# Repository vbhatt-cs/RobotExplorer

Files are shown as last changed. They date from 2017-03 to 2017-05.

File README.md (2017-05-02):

# Scout Car for Automatic Mapping

Scout car for automatic mapping is a bot which can explore and map an area automatically.

## Requirements

### Hardware
  * Arduino WeMos D1 R2 (any arduino with WiFi shield works but pin mapping and arduino code will change)
  * 12V battery
  * 2 DC motors + wheels
  * L298N motor driver
  * Wheel encoder with IR sensor 
  * IR proximity sensor 
  * MPU 9250 9-dof imu sensor
  * Chassis to mount the components
  
### Software
  * Arduino IDE - https://www.arduino.cc/en/main/software
  * Optional - Microsoft Visual Studio + Visual Micro - https://www.visualstudio.com/downloads/ http://www.visualmicro.com/page/Arduino-Visual-Studio-Downloads.aspx
  * Python 3.x (tested with 3.6) - https://www.python.org/downloads/
  * socket, parse, numpy, matplotlib libraries
    
Socket is installed by default in most python distributions. For other libraries, use the command 

    pip install <library_name>
    
## Getting Started

First, connect the componenets according to the below diagram

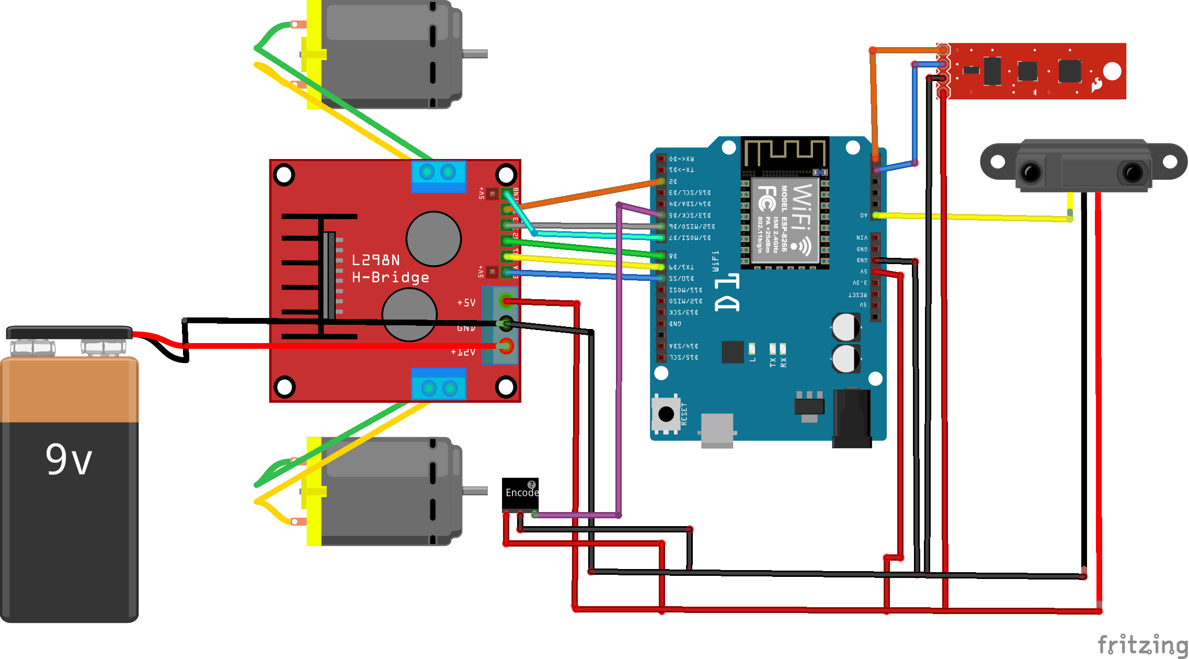
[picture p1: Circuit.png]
Ciruit


Note that the battery should be 12V. The red component on the top right is MPU9250 and the component below it is the IR sensor. The pin numbers on the WeMos might be different from what is given in the diagram. Physically the connections look the same (Ex.: the wire connected to the second pin from the top in the diagram will be connected to the second pin from the top in WeMos)

Once the hardware connections are done, open the [ino file](V1_1_MoveInGivenDirectionWemos/V1_1_MoveInGivenDirectionWemos/V1_1_MoveInGivenDirectionWemos.ino) (if you are using visual studio, open the [visual studio solution](V1_1_MoveInGivenDirectionWemos/V1_1_MoveInGivenDirectionWemos.sln)). Build and upload to the WeMos board (see this [tutorial](http://www.instructables.com/id/Programming-the-WeMos-Using-Arduino-SoftwareIDE/) if you haven't programmed WeMos before).

Now, connect to WeMos wifi network from your PC and run the [main python script](PCSide/main.py). If everything works fine, you should be seeing the bot moving around and a map being generated on the PC. After exploration, the map will be saved in the same folder ([Example](PCSide/map.png)). If there is some problem, see the troubleshooting section.

## Troubleshooting

1. **No WiFi network of WeMos**: Check if the bot is on and LED of the WiFi shield in WeMos is glowing. If not, reset WeMos and check again. If it still doesn't work, then try uploading the [WeMos Web Server](TempCodes/Wemos_WebServer) project and check if it works. If it fails then there is some problem with the WiFi shield.

2. **The bot continuously rotates in one place or it doesn't move in the right direction**: The magnetometer is most probably not calibrated properly. Upload the [Calibration](TempCodes/MPU9250_Yaw) project and open the serial monitor. Reset WeMos and move the bot in shape of 8 (like during compass calibration in phones) or just rotate around all 3 axes (*Note that the calibration needs to be done away from strong magnets and when the magnetometer is mounted on the bot*). After a while, the yaw values will be displayed in the serial monitor. Check if they are correct. If so, copy the bias, scale values to the main ino file (into magBias and magScale). If not, reset and try again. 

    In case the calibration fails after multiple attempts, print mx, my, mz values from magnetometer and copy them to an excel sheet. Find min, max value of mx, my, and mz. Find bias = (max + min)/2 and scale = (max - min)/2 for x, y, and z. 
    Calculate x' = (x - biasX)/scaleX, and similarly y' and z'. Scatter plot x', y', z' pairwise and check if they are points in the interior of a unit circle. If so, then use the bias, scale values. Else, repeat the calibration.
    
    In the unlikely case that the yaw values are not stable, change the values of Kp, Ki in MahonyQuaternionUpdate function till it gives stable values quickly and then do the calibration.
    
3. **The bot stops (and detects wall) even if the wall is far**: Check the trigger range of IR proximity sensor and set it such that the bot has enough space to rotate after detecting the wall. IR proximity sensor is known to give bad readings in the presence of sunlight. So it is better to block sunlight during mapping. If you need to bot to map outdoor environment, then a different sensor should be used to detect walls.

4. **The bot moves very near/ very far at a time**: Set the CELL_DIS in [maparray.py](PCSide/maparray.py) higher/lower.

5. **The bot doesn't map the full area**: Set the MAP_SIZE to a higher value.
    
4. **The bot moves very slowly/ one of the wheels doesn't turn**: The battery is getting discharged. Replace/recharge them. 

5. **UDP connection times out**: It may happen due to multiple reasons. First, open the serial monitor and reset WeMos to see whether it is creating a WiFi hotspot. Also, check if the IP address of WeMos is same as the one written in [communication.py](PCSide/communication.py) and run again. Second, replace/recharge the battery. Third, in [main.py](PCSide/main.py), increase the delay such that the bot is able to move and stop before a new UDP request is sent by the PC (5 seconds is generally enough) and run again. If neither of the methods work, then the reason is unknown.

## Known issues

1. WeMos doesn't reset when it is connected to the encoder (through D3 pin). A temporary fix is to remove the connection, reset the board and connect the encoder afterwards.

2. Connection between PC and bot times out sometimes. The timeout is extremely rare when the battery is fully charged and there are no other strong WiFi networks in the surrounding. Other observations were - 
    * Timeouts are less frequent when the delay between two consecutive requests by the PC is high
    * More timeouts when an UDP packet reaches arduino while the motor is moving
    * No timeouts when only UDP communication is taking place (no sensors/motor)
    * No timeouts when encoder is removed (not fully tested - might just be coincidence)

3. There are oscillations when the bot rotates in place. This can be solved by turning the bot slowly so that there is no overshoot.

4. The bot can deviate from its path due to incorrect rotation/movement.

5. If the bot deviates a bit and wrongly detects a wall (physically) in the cell (of the map) which it had previously detected as open, then the bot gets stuck there and the mapping doesn't continue.

6. If the proximity sensor fails to detect a wall (due to not being in the line of sight) and the bot crashes into it, it can't recover and continue mapping.

## Future work

1. **Solving existing issues**: Using a motor with finer speed control solves the first issue. The second issue is solved partially by using encoders in addition to magnetometer for rotation and is fully solved if the PC code is able to detect wrong movement and correct it. The third issue won't occur if the bot movement is correct. Fourth issue can be solved by adding more sensors around the bot (it still can't recover from physical crashes)

2. **Reducing power consumption**: Right now, the exact power usage is not calculated and the hardware/code is not optimized for minimum power consumption. It will be necessary since the bot should be able to map the required area in a single charge.

3. **Mapping/Exploration which doesn't depend on accurate movement**: The idea of this bot may be used for applications like cleaning the house where it may not be possible to move the bot accurately due to its size. Also, the resolution of the map will be bad if the bot is assumed to be smaller than or equal to one cell size. Hence, the bot needs to be able to explore/map in arbitrary directions.

4. **Dynamic updation of map**: Right now, the bot assumes the area to map as static and generates a map. But in reality, there may be obstacles which are moved around and hence, the map needs to be changed dynamically.

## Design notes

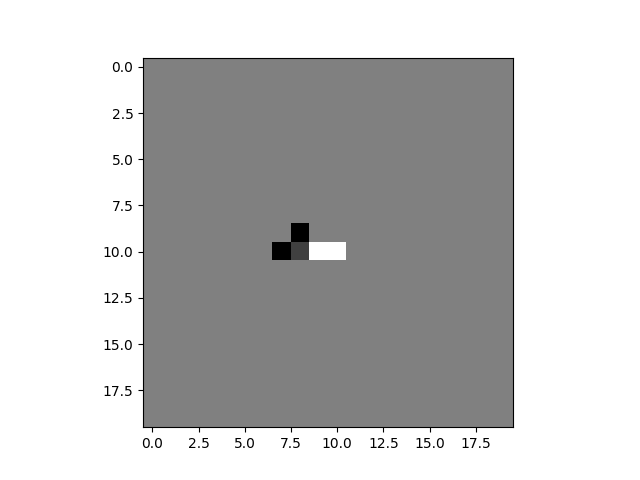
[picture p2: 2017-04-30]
PCSide/map.png

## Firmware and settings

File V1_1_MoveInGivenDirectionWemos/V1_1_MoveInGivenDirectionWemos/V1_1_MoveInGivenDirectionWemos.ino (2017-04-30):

/*
Name:		V1_1_MoveInGivenDirectionWemos.ino
Created:	3/11/2017 11:35:00 AM
Author:	Varun Bhatt
*/

#include <PID_v1.h>				//Arduino PID library
//For magnetometer
#include <Wire.h>
#include <FaBo9Axis_MPU9250.h>
//For web server
#include <ESP8266WiFi.h>
#include <WiFiUdp.h>

//Set to 1 if debugging in serial
const bool DEBUG_SERIAL = 1;

// Pins used on Wemos D1 R2
#define LPWM D8
#define LDIR1 D7
#define LDIR2 D6

#define RPWM D5
#define RDIR1 D4
#define RDIR2 D0

#define ENCODER D3

#define PROXIMITY A0

// Left and Right steady state speed
const int RIGHT_SS_SPEED = 300;
const int LEFT_SS_SPEED = 300;
const int CONSTRAIN_LOW = 250;
const int CONSTRAIN_HIGH = 350;

// Left and Right speed
int rightSpeed = 300;
int leftSpeed = 300;

//PID Values
double curDirection = 0, output;

// PID Multipliers
float kp = 1;
float ki = 0;
float kd = 0.2;

double setDirection = 0;	//Reference direction
int setDistance = 0;		//Reference distance

int curDistance = 0;
bool runMotor = true;
bool rotateMotor = true;
bool wall = false;
bool startFlag = true;

FaBo9Axis fabo_9axis;	// For MPU9250 readings
float q[4] = { 1.0f, 0.0f, 0.0f, 0.0f };    // vector to hold quaternion
float eInt[3] = { 0.0f, 0.0f, 0.0f };       // vector to hold integral error for Mahony method
float deltat = 0.0f;						// integration interval for both filter schemes
uint32_t lastUpdate = 0;	// used to calculate integration interval
uint32_t Now = 0;							// used to calculate integration interval
uint32_t startTime = 0;
float magBias[3] = { 7.49, 3.28, -18.94};
float magScale[3] = { 39.96, 41.53, 33.60};

//Setup PID
PID wheelControl(&curDirection, &output, &setDirection, kp, ki, kd, DIRECT);

//SSID of access point
const char *SSID = "Wemos";
const char *password = "qwer321!";

//UDP stuff
WiFiUDP Udp;
//IPAddress ip(192, 168, 137, 69);
//IPAddress gateway(192, 168, 137, 1);
//IPAddress subnet(255, 255, 255, 0);
unsigned int localUdpPort = 4210;  // local port to listen on

void setup() {
	if (DEBUG_SERIAL)
		Serial.begin(9600);

    pinMode(ENCODER, INPUT);
    attachInterrupt(digitalPinToInterrupt(ENCODER), encISR, FALLING);

	pinMode(RPWM, OUTPUT);
	pinMode(RDIR1, OUTPUT);
	pinMode(RDIR2, OUTPUT);

	pinMode(LPWM, OUTPUT);
	pinMode(LDIR1, OUTPUT);
	pinMode(LDIR2, OUTPUT);

	pinMode(PROXIMITY, INPUT);

	//Start the WiFi access point
	if (DEBUG_SERIAL)
	{
		Serial.println();
		Serial.print("Configuring access point...");
	}

	WiFi.softAP(SSID);
	/*WiFi.begin(SSID, password);
	WiFi.config(ip, gateway, subnet);

	while (WiFi.status() != WL_CONNECTED) {
		delay(500);
		if (DEBUG_SERIAL)
			Serial.print(".");
	}*/

	Udp.begin(localUdpPort);

	if (DEBUG_SERIAL)
		Serial.printf("Now listening at IP %s, UDP port %d\n", WiFi.softAPIP().toString().c_str(), localUdpPort);
    
	//Stop the motor initially
	digitalWrite(LDIR1, LOW);
	digitalWrite(LDIR2, LOW);
	analogWrite(LPWM, 0);
	digitalWrite(RDIR1, LOW);
	digitalWrite(RDIR2, LOW);
	analogWrite(LPWM, 0);

	//Initialize MPU9250
	fabo_9axis.begin();

	//turn the PID on
	wheelControl.SetOutputLimits(-1000, 1000);
	wheelControl.SetMode(AUTOMATIC);

	startTime = micros();
}

void loop() {
	handleUDP();	//Handle UDP messages

	//Read MPU9250 and get compass heading
	Now = micros();
	deltat = ((Now - lastUpdate) / 1000000.0f); // set integration time by time elapsed since last filter update
	lastUpdate = Now;
	
	curDirection = getYaw();
	if (curDirection < -170)
		curDirection = abs(curDirection);

	runMotor = curDistance < setDistance;

	if (rotateMotor)
		wall = false;
	else
		wall = analogRead(PROXIMITY) < 512;

	//Compute the PID output
	wheelControl.Compute();

	if (DEBUG_SERIAL)
	{
		Serial.print(" yaw = "); Serial.println(curDirection);
		Serial.print(" ref = "); Serial.println(setDirection);
		Serial.print(" output = "); Serial.println(output);
		Serial.print(" distance = "); Serial.println(curDistance);
	}

	//Set the PWM values for the motor
	//
	//Output added to one wheel and subtracted from another wheel to rotate the bot
	//Change the sign of output (if needed) to make the bot rotate in a direction which reduces the error. 
	//
	//The motor was not moving for PWM below CONSTRAIN_LOW and moving too fast for PWM over CONSTRAIN_HIGH
	//So constrain the value inside that range
	rightSpeed = RIGHT_SS_SPEED + output;
	rightSpeed = constrain(rightSpeed, CONSTRAIN_LOW, CONSTRAIN_HIGH);

	leftSpeed = LEFT_SS_SPEED - output;
	leftSpeed = constrain(leftSpeed, CONSTRAIN_LOW, CONSTRAIN_HIGH);

	if (runMotor && !wall)	//Start the motor
	{
		if (micros() - startTime < 8000000)
		{
			analogWrite(RPWM, 0);
			analogWrite(LPWM, 0);
		}

		else if ((abs(setDirection - curDirection) > 5 && abs(setDirection - curDirection) < 355) && rotateMotor)
		{
			if (setDirection - curDirection > 0 && setDirection - curDirection < 180)
			{
				digitalWrite(RDIR2, LOW);
				digitalWrite(RDIR1, HIGH);
				digitalWrite(LDIR2, LOW);
				digitalWrite(LDIR1, HIGH);
				analogWrite(RPWM, RIGHT_SS_SPEED);
				analogWrite(LPWM, LEFT_SS_SPEED);
			}
			else
			{
				digitalWrite(LDIR1, LOW);
				digitalWrite(LDIR2, HIGH);
				digitalWrite(RDIR1, LOW);
				digitalWrite(RDIR2, HIGH);
				analogWrite(RPWM, RIGHT_SS_SPEED);
				analogWrite(LPWM, LEFT_SS_SPEED);
			}
		}
		else
		{
			rotateMotor = false;
			digitalWrite(LDIR1, LOW);
			digitalWrite(LDIR2, HIGH);
			digitalWrite(RDIR2, LOW);
			digitalWrite(RDIR1, HIGH);
			analogWrite(RPWM, rightSpeed);
			analogWrite(LPWM, leftSpeed);
		}
	}
	else	//Stop the motor
	{
		digitalWrite(LDIR1, LOW);
		digitalWrite(LDIR2, LOW);
		analogWrite(LPWM, 0);
		digitalWrite(RDIR1, LOW);
		digitalWrite(RDIR2, LOW);
		analogWrite(LPWM, 0);
	}

	myDelay(200);
}

void myDelay(int ms) {
    while(ms--) {
        if((!runMotor || wall) && !startFlag)
            return;
        runMotor = curDistance < setDistance;
        if (rotateMotor)
            wall = false;
        else
            wall = analogRead(PROXIMITY) < 512;
        delay(1);
    }
}

//Handle UDP request
void handleUDP() {
	int packetSize = Udp.parsePacket();
	if (packetSize)
	{
		// receive incoming UDP packets
		char incomingPacket[2048];
		int len = Udp.read(incomingPacket, 2048);
		if (len > 0)
		{
			incomingPacket[len] = 0;
		}

		if (DEBUG_SERIAL)
		{
			Serial.printf("Received %d bytes from %s, port %d\n", packetSize, Udp.remoteIP().toString().c_str(), Udp.remotePort());
			Serial.printf("UDP packet contents: %s\n", incomingPacket);
		}

		String req(incomingPacket);

		// send back a reply, to the IP address and port we got the packet from
		// Sensor data requested
		if (req == "Sensors")
		{
			String reply = String(curDirection) + " " + curDistance + " " + wall + " " + (!runMotor);
			Udp.beginPacket(Udp.remoteIP(), Udp.remotePort());
			Udp.write(reply.c_str());
			Udp.endPacket();
		}
		//New movement command
		else
		{
			String dir, dis;
			dir = req.substring(0, req.indexOf(' '));
			dis = req.substring(req.indexOf(' ') + 1);

			float setDirOld = setDirection;
			setDirection = dir.toFloat();
			setDistance = dis.toInt();

			if (setDistance > 0)
				curDistance = 0;

            startFlag = false;

			if(setDirection != setDirOld)
				rotateMotor = true;

			if (DEBUG_SERIAL)
			{
				Serial.println("$$$$$$$$$$$$$$$$$$$");
				Serial.print(setDirection);
				Serial.print(" ");
				Serial.println(setDistance);
				Serial.println("$$$$$$$$$$$$$$$$$$$");
			}
		}
	}
}

float getYaw()
{
	float ax, ay, az;
	float gx, gy, gz;
	float mx, my, mz;

	fabo_9axis.readAccelXYZ(&ax, &ay, &az);
	fabo_9axis.readGyroXYZ(&gx, &gy, &gz);
	fabo_9axis.readMagnetXYZ(&mx, &my, &mz);

	mx = (mx - magBias[0]) / magScale[0];
	my = (my - magBias[1]) / magScale[1];
	mz = (mz - magBias[2]) / magScale[2];

	/////////
	//Serial.print("mx: ");
	//Serial.print(mx);
	//Serial.print(" my: ");
	//Serial.print(my);
	//Serial.print(" mz: ");
	//Serial.println(mz);

	/*if (DEBUG_SERIAL)
	{
	Serial.print("ax: ");
	Serial.print(ax);
	Serial.print(" ay: ");
	Serial.print(ay);
	Serial.print(" az: ");
	Serial.println(az);
	Serial.print("gx: ");
	Serial.print(gx);
	Serial.print(" gy: ");
	Serial.print(gy);
	Serial.print(" gz: ");
	Serial.println(gz);
	Serial.print("mx: ");
	Serial.print(mx);
	Serial.print(" my: ");
	Serial.print(my);
	Serial.print(" mz: ");
	Serial.println(mz);
	Serial.print("q0 = "); Serial.print(q[0]);
	Serial.print(" qx = "); Serial.print(q[1]);
	Serial.print(" qy = "); Serial.print(q[2]);
	Serial.print(" qz = "); Serial.println(q[3]);
	}*/

	MahonyQuaternionUpdate(ax, ay, az, gx*PI / 180.0f, gy*PI / 180.0f, gz*PI / 180.0f, my, mx, mz);

	float yaw = atan2(2.0f * (q[1] * q[2] + q[0] * q[3]), q[0] * q[0] + q[1] * q[1] - q[2] * q[2] - q[3] * q[3]);
	yaw *= 180.0f / PI;

	return yaw;
}

void MahonyQuaternionUpdate(float ax, float ay, float az, float gx, float gy, float gz, float mx, float my, float mz)
{
	// these are the free parameters in the Mahony filter and fusion scheme, Kp for proportional feedback, Ki for integral
	const float Kp = 5.0f;
	const float Ki = 0.1f;

	float q1 = q[0], q2 = q[1], q3 = q[2], q4 = q[3];   // short name local variable for readability
	float norm;
	float hx, hy, bx, bz;
	float vx, vy, vz, wx, wy, wz;
	float ex, ey, ez;
	float pa, pb, pc;

	// Auxiliary variables to avoid repeated arithmetic
	float q1q1 = q1 * q1;
	float q1q2 = q1 * q2;
	float q1q3 = q1 * q3;
	float q1q4 = q1 * q4;
	float q2q2 = q2 * q2;
	float q2q3 = q2 * q3;
	float q2q4 = q2 * q4;
	float q3q3 = q3 * q3;
	float q3q4 = q3 * q4;
	float q4q4 = q4 * q4;

	// Normalise accelerometer measurement
	norm = sqrtf(ax * ax + ay * ay + az * az);
	if (norm == 0.0f) return; // handle NaN
	norm = 1.0f / norm;        // use reciprocal for division
	ax *= norm;
	ay *= norm;
	az *= norm;

	// Normalise magnetometer measurement
	norm = sqrtf(mx * mx + my * my + mz * mz);
	if (norm == 0.0f) return; // handle NaN
	norm = 1.0f / norm;        // use reciprocal for division
	mx *= norm;
	my *= norm;
	mz *= norm;

	// Reference direction of Earth's magnetic field
	hx = 2.0f * mx * (0.5f - q3q3 - q4q4) + 2.0f * my * (q2q3 - q1q4) + 2.0f * mz * (q2q4 + q1q3);
	hy = 2.0f * mx * (q2q3 + q1q4) + 2.0f * my * (0.5f - q2q2 - q4q4) + 2.0f * mz * (q3q4 - q1q2);
	bx = sqrtf((hx * hx) + (hy * hy));
	bz = 2.0f * mx * (q2q4 - q1q3) + 2.0f * my * (q3q4 + q1q2) + 2.0f * mz * (0.5f - q2q2 - q3q3);

	// Estimated direction of gravity and magnetic field
	vx = 2.0f * (q2q4 - q1q3);
	vy = 2.0f * (q1q2 + q3q4);
	vz = q1q1 - q2q2 - q3q3 + q4q4;
	wx = 2.0f * bx * (0.5f - q3q3 - q4q4) + 2.0f * bz * (q2q4 - q1q3);
	wy = 2.0f * bx * (q2q3 - q1q4) + 2.0f * bz * (q1q2 + q3q4);
	wz = 2.0f * bx * (q1q3 + q2q4) + 2.0f * bz * (0.5f - q2q2 - q3q3);

	// Error is cross product between estimated direction and measured direction of gravity
	ex = (ay * vz - az * vy) + (my * wz - mz * wy);
	ey = (az * vx - ax * vz) + (mz * wx - mx * wz);
	ez = (ax * vy - ay * vx) + (mx * wy - my * wx);
	if (Ki > 0.0f)
	{
		eInt[0] += ex;      // accumulate integral error
		eInt[1] += ey;
		eInt[2] += ez;
	}
	else
	{
		eInt[0] = 0.0f;     // prevent integral wind up
		eInt[1] = 0.0f;
		eInt[2] = 0.0f;
	}

	// Apply feedback terms
	gx = gx + Kp * ex + Ki * eInt[0];
	gy = gy + Kp * ey + Ki * eInt[1];
	gz = gz + Kp * ez + Ki * eInt[2];

	// Integrate rate of change of quaternion
	pa = q2;
	pb = q3;
	pc = q4;
	q1 = q1 + (-q2 * gx - q3 * gy - q4 * gz) * (0.5f * deltat);
	q2 = pa + (q1 * gx + pb * gz - pc * gy) * (0.5f * deltat);
	q3 = pb + (q1 * gy - pa * gz + pc * gx) * (0.5f * deltat);
	q4 = pc + (q1 * gz + pa * gy - pb * gx) * (0.5f * deltat);

	// Normalise quaternion
	norm = sqrtf(q1 * q1 + q2 * q2 + q3 * q3 + q4 * q4);
	if (norm == 0.0f) return; // handle NaN
	norm = 1.0f / norm;
	q[0] = q1 * norm;
	q[1] = q2 * norm;
	q[2] = q3 * norm;
	q[3] = q4 * norm;

}

void encISR()
{
	if (!rotateMotor)
		curDistance++;
}

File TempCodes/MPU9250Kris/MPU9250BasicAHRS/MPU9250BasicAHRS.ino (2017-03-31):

/* MPU9250 Basic Example Code
 by: Kris Winer
 date: April 1, 2014
 license: Beerware - Use this code however you'd like. If you 
 find it useful you can buy me a beer some time.
 
 Demonstrate basic MPU-9250 functionality including parameterizing the register addresses, initializing the sensor, 
 getting properly scaled accelerometer, gyroscope, and magnetometer data out. Added display functions to 
 allow display to on breadboard monitor. Addition of 9 DoF sensor fusion using open source Madgwick and 
 Mahony filter algorithms. Sketch runs on the 3.3 V 8 MHz Pro Mini and the Teensy 3.1.
 
 SDA and SCL should have external pull-up resistors (to 3.3V).
 10k resistors are on the EMSENSR-9250 breakout board.
 
 Hardware setup:
 MPU9250 Breakout --------- Arduino
 VDD ---------------------- 3.3V
 VDDI --------------------- 3.3V
 SDA ----------------------- A4
 SCL ----------------------- A5
 GND ---------------------- GND
 
 Note: The MPU9250 is an I2C sensor and uses the Arduino Wire library. 
 Because the sensor is not 5V tolerant, we are using a 3.3 V 8 MHz Pro Mini or a 3.3 V Teensy 3.1.
 We have disabled the internal pull-ups used by the Wire library in the Wire.h/twi.c utility file.
 We are also using the 400 kHz fast I2C mode by setting the TWI_FREQ  to 400000L /twi.h utility file.
 */
#include <SPI.h>
#include <Wire.h>   
//#include <Adafruit_GFX.h>
//#include <Adafruit_PCD8544.h>

// Using NOKIA 5110 monochrome 84 x 48 pixel display
// pin 9 - Serial clock out (SCLK)
// pin 8 - Serial data out (DIN)
// pin 7 - Data/Command select (D/C)
// pin 5 - LCD chip select (CS)
// pin 6 - LCD reset (RST)
//Adafruit_PCD8544 display = Adafruit_PCD8544(9, 8, 7, 5, 6);

// See also MPU-9250 Register Map and Descriptions, Revision 4.0, RM-MPU-9250A-00, Rev. 1.4, 9/9/2013 for registers not listed in 
// above document; the MPU9250 and MPU9150 are virtually identical but the latter has a different register map
//
//Magnetometer Registers
#define AK8963_ADDRESS   0x0C
#define AK8963_WHO_AM_I  0x00 // should return 0x48
#define AK8963_INFO      0x01
#define AK8963_ST1       0x02  // data ready status bit 0
#define AK8963_XOUT_L	 0x03  // data
#define AK8963_XOUT_H	 0x04
#define AK8963_YOUT_L	 0x05
#define AK8963_YOUT_H	 0x06
#define AK8963_ZOUT_L	 0x07
#define AK8963_ZOUT_H	 0x08
#define AK8963_ST2       0x09  // Data overflow bit 3 and data read error status bit 2
#define AK8963_CNTL      0x0A  // Power down (0000), single-measurement (0001), self-test (1000) and Fuse ROM (1111) modes on bits 3:0
#define AK8963_ASTC      0x0C  // Self test control
#define AK8963_I2CDIS    0x0F  // I2C disable
#define AK8963_ASAX      0x10  // Fuse ROM x-axis sensitivity adjustment value
#define AK8963_ASAY      0x11  // Fuse ROM y-axis sensitivity adjustment value
#define AK8963_ASAZ      0x12  // Fuse ROM z-axis sensitivity adjustment value

#define SELF_TEST_X_GYRO 0x00                  
#define SELF_TEST_Y_GYRO 0x01                                                                          
#define SELF_TEST_Z_GYRO 0x02

/*#define X_FINE_GAIN      0x03 // [7:0] fine gain
#define Y_FINE_GAIN      0x04
#define Z_FINE_GAIN      0x05
#define XA_OFFSET_H      0x06 // User-defined trim values for accelerometer
#define XA_OFFSET_L_TC   0x07
#define YA_OFFSET_H      0x08
#define YA_OFFSET_L_TC   0x09
#define ZA_OFFSET_H      0x0A
#define ZA_OFFSET_L_TC   0x0B */

#define SELF_TEST_X_ACCEL 0x0D
#define SELF_TEST_Y_ACCEL 0x0E    
#define SELF_TEST_Z_ACCEL 0x0F

#define SELF_TEST_A      0x10

#define XG_OFFSET_H      0x13  // User-defined trim values for gyroscope
#define XG_OFFSET_L      0x14
#define YG_OFFSET_H      0x15
#define YG_OFFSET_L      0x16
#define ZG_OFFSET_H      0x17
#define ZG_OFFSET_L      0x18
#define SMPLRT_DIV       0x19
#define CONFIG           0x1A
#define GYRO_CONFIG      0x1B
#define ACCEL_CONFIG     0x1C
#define ACCEL_CONFIG2    0x1D
#define LP_ACCEL_ODR     0x1E   
#define WOM_THR          0x1F   

#define MOT_DUR          0x20  // Duration counter threshold for motion interrupt generation, 1 kHz rate, LSB = 1 ms
#define ZMOT_THR         0x21  // Zero-motion detection threshold bits [7:0]
#define ZRMOT_DUR        0x22  // Duration counter threshold for zero motion interrupt generation, 16 Hz rate, LSB = 64 ms
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

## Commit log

2017-03-09 Motor PID with magnetometer V1
2017-03-11 Combined arduino (mx as reference) code
2017-03-11 Wemos combined code (without angle and encoder)
2017-03-12 Calibration; Pretty much everything working
    [MagCal.xlsx]
2017-03-31 Demo final
    [MagCal.xlsx, Yaw.xlsx]
2017-04-12 Arduino code for proximity sensor, UDP
2017-04-12 Arduino code for proximity, UDP
2017-04-13 Wifi not working. Rotation not proper. Rest fine
    [MPU9250_Yaw.ino, V1_1_MoveInGivenDirectionWemos.ino]
2017-04-13 Working overall. Rotation near wall is inconsistent (probably due to sensor placement)
2017-04-22 Local IP, save map in PCSide. Faster loop in arduino
    [Calib.xlsx]
2017-04-30 Circuit added
    [Circuit_Fritzing.fzz]
